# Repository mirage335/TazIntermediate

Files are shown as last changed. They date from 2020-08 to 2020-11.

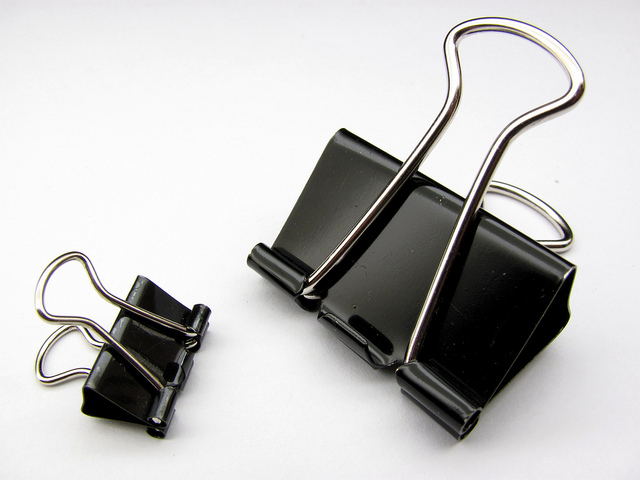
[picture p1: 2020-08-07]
_experimental/0100-Bundle/0165-Slab-slabAlternative-binderClipShim/_ref/BinderClip-f2otZE/orig/binder-clip.jpg

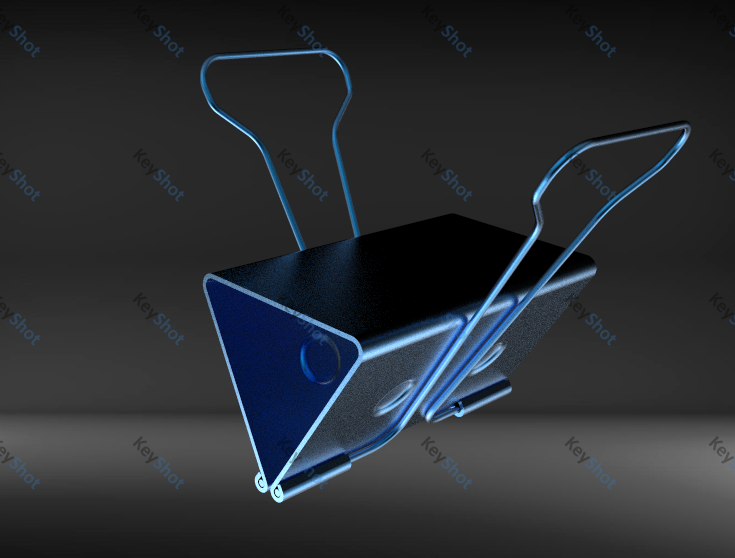
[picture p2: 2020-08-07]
_experimental/0100-Bundle/0165-Slab-slabAlternative-binderClipShim/_ref/BinderClip-f2otZE/orig/Capture.PNG

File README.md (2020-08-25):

Copyright (C) 2020- mirage335
See the end of the file for license conditions.
See license.txt for TazIntermediate license conditions.

A 3D printer system prioritizing cost-effectiveness and familiarity for industrial users accustomed to LulzBot Taz printers. Designed to balance similar or only slightly higher capital cost for for higher throughput, higher quality, and substantially lower maintence.

# Usage

Step-by-step assembly and maintenance instructions are provided, derived from the detailed design files.

Please read "_doc/TazIntermediate_serviceManual.pdf" .

# Distribution

REPUTABLE PROVIDERS OF TazIntermediate HARDWARE AND DESIGN FILES SHOULD INCLUDE IN YOUR ORDER A VERIFIABLE SERIAL NUMBER, GIT HASH, AND FULL COPY OF THE DESIGN FILES WITH ANY MODIFICATIONS.

Beware many of the assembly steps require careful attention to preloading, equal length cuts, strict order of operations, and correct alloy/tempering, among other things, for expected precision, accuracy, and durability. Intentionally little redundancy is available to compensate for poor quality components.

Consider providing end-users an entire copy of this repository with all submodules, in addition to PDF documents. Physical SDCard/USB flash devices may be suitable for the repository, printed hardcopy may be suitable for the PDF documents.

# Design

Inspired by the LulzBot Taz5 printer. Substantially similar to TazStiff, TazUp, Taz_Mega. TazIntermediate mostly serves to reduce new assembly time and wiring complexity.

Existing TazStiff printers should continue to offer similar performance and maintenance characteristics to TazIntermediate printers.

# Redistribution and Preservation

Entire 'recursive' clones of this repository with all submodules may be appropriate for redistribution and preservation.

# Safety

INTENDED FOR INDUSTRIAL USERS.
Internal wiring layout differs significantly from typical consumer 3D printers. In particular, contrary to typical RAMBo motherboard expectations, Vsys directly from PSU is used for Hotend power, and may be unfused. Reverse connection may present unfused (all RAMBo motherboard fuses bypassed) short-circuit load exceeding 20A, severely overloading MOSFET, wiring, and connectors.

Consider adding fiberglass or silica high-temperature sleeving to wiring near hotend.

Use external balancer with LiPo batteries. Cheaply available from HobbyKing among other places.

Not Ethernet compatible, will destroy network hardware.

Do not unplug powered steppers.

Beware common grounding and other wiring issues.

ClassIV lasers are extraordinarily hazardous. Backscatter from the projected spot alone is sufficient to slice a retina. Avoid exposure, and wear eye protection.

Ground-referenced voltage (ie. wall current) applied to Vsys/Vee is NOT guaranteed to remain isolated from other circuits. Spark gap surge protectors specifically, among other faults, are expected to allow sustained connection of high-voltage ground-referenced current to all other circuits.

Testing all essential high current circuits to 30% above requirements is recommended. Such testing has not necessarily been performed. Any particular circuit may not have been designed to accommodate any significant current carrying capacity. Oil immersion may increase useful ampacity, though the risk of dissolution or fire must be considered carefully. Design goals are made on a best effort basis only, suggested but not guaranteed for further development, particularly for short narrow traces.
GenericRap and derivative PCBs - Typically 5A power. Between XT60 Connectors, 40A power.
Solderless Breadboard - Typically 3A per contact. Typically >6A total to gold, tin, lead or similarly plated square pin header 'power feeder' as used by GenericRap.
Wrapping Wire 30AWG "Kynar" Insulated - Typically 6A per wire.

Fire suppression or low flammability products may be mentioned for consideration of further development only. None are specifically recommended for any situation, none may have been tested in any relevant application, and no claim of effectiveness is made.

No claim of liability is made by anyone. Your accident is your accident. Use common sense, and follow all regulations. If you don't understand the safety features and limitations, don't use this circuitry or anything similar.

# FutureWork

# Reference

https://en.wikipedia.org/wiki/Point-to-point_construction

https://www.mcmaster.com/high-temperature-sleeving/

https://www.mcmaster.com/high-temperature-sleeving/fiberglass-high-temperature-sleeving/

https://www.mcmaster.com/high-temperature-sleeving/expandable-electrical-insulating-tube-sleeving/

https://e3d-online.com/products/fibreglass-sleeving-for-insulating-thermistors-100mm

https://www.mcmaster.com/high-temperature-sleeving/silica-high-temperature-sleeving/

# Directory Specification

Consider keeping a copy of this specification alongside relevant projects for reference.

Please regard as a loose specification intended to offer unallocated regions for expansion and subordinate to any improvements that may be found in actual implementations.

Projects which may be assembled into larger projects, if sufficiently well-developed, should include their own appropriate directories, rather than referencing files shared within larger projects. That is to say, a sort of 'static linking' approach is strongly recommended.

Numbered directories with '[z]-' in their prefix and a '/' may substitute the '/' for either a '-' or separate directories.

Numbered directories of top-directories may be placed alongside top-directories if desired. Numbering scheme is intended to minimize conflicts.

Templates should populate only the most usual directories. Not all directories need be populated for a project.

```

_lib	- software, records, etc, typically uniquely needed by specific CAD model

00[00]-RESERVED (do NOT use)

01[00]-Bundle
	0110-Frames
	0150-Actuators
	0151[z]-Thruster/Driver
		Components only used for these?
		Screws used within these?
	0160-Tools
		Nozzle
		Hot-End
		Cold-End
		Extension (Bowden Tube)
	0162-Supplementary
		Filament Storage
	0165-Slab (workpiece mounting surface)
	0170-Tray (surface to mount electronics and similar)
	0172-Rack (enclosure for electronics and similar, and/or junction box)
	0175-Cabinet (arbitrary storage)

11[00]-Structural (Passive, Cut To Size)
	1110[z]-Extrusions/Timbers
		_resized
	1112[z]-Sheets/Panels/Plates (for frames only)
		_rescaled (PreDrilled only)
	1115-Backing (Table)

30[00]-Conveyance
	3030[z]-Shaft/Piston
	3032-LeadScrew
	3033[z]-Belts
	3035- to 3038- RESERVED (do NOT use)

35[00]-Couplings (including flexible, u-joints, etc)
	3530-LeadScrew_to_Motor

50[00]-Effectors
	5050[z]-Motors/Steppers/Servos
	5051[z]-RotaryBearings/RotaryShims
	
	5052[z]-NutBlocks/PlatesEffectors/BracketsEffectors (typically belt tie-down points), etc.
	5053-RESERVED
	
	5054[z]-Guides (Wheels/Bushings/LinearBearings)
	
	5055-Pulleys
	5056-Gears
	
	5058-Limit Switch

55[00]-RESERVED (do NOT use)

(6000 RESERVED)

(7000 RESERVED)

80[00]-Endpoints
	8080-Plug
		RJ45
		misc
	8081-Jack
		RJ45
		misc
	8082-RESERVED (do NOT use)
	8083-RESERVED (do NOT use)

85[00]-Dissipator
	8580-Fans
	8581-Pump
	8582-Heatsink
	8585-Radiator

9000-Miscellaneous
	9090z-Screws/Bolts
	9095-frequent (most frequently used)
	9099-Misc
		zMisc (unsortred, typically uniquely needed by specific CAD model)

9100-KEEPOUT (solid objects used to mark regions reserved for future use)

94[00]
to
98[00]
	RESERVED for future use

99[00]-import
	RESERVED for future use

```

# Third-Party Copyright Notices

Third-Party copyrights are noted within text files alongside directories containing the original files, and/or within text files alongside directories containing the modified files, and/or within version control commit history.

Some copyright licenses have specific requirements, and some authors have specific requests, to prominently display copyright notices - these are included here.

However, the manner some or all of these third-party files are used may in fact be fair use, in which case the third-party licenses would not in fact have any effect on the license requirements for the otherwise possibly derivative project.

"
This design incorporates OpenBuilds, LLC design work(s) shared Open Source under the CC BY-SA 4.0 License.
"

# Copyright

This file is part of TazIntermediate.

TazIntermediate is free software: you can redistribute it and/or modify
it under the terms of the GNU General Public License as published by
the Free Software Foundation, either version 3 of the License, or
(at your option) any later version.

TazIntermediate is distributed in the hope that it will be useful,
but WITHOUT ANY WARRANTY; without even the implied warranty of
MERCHANTABILITY or FITNESS FOR A PARTICULAR PURPOSE.  See the
GNU General Public License for more details.

You should have received a copy of the GNU General Public License
along with TazIntermediate.  If not, see <http://www.gnu.org/licenses/>.

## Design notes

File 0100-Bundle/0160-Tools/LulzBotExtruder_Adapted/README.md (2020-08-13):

'Stock' is expected to be workable as-is, though rigidity might be a little less due to use of plastic. This may or may not be significant.

'Bare' strictly considered experimental due to imprecise cooling mounting dimensions due to lack of matching accurate blower fan model for reference. Also for this reason the 'LulzBotExtruder_Block' has not been exported to other formats (ie. STEP, STL).

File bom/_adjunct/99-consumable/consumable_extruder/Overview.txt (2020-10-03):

ATC Semitec 104GT-2
	UNPROVEN - https://www.amazon.com/Gikfun-Semitic-104GT-2-Thermistor-Printer/dp/B00UFBIRVI/

6mm x 20mm 24V Heater Cartridge >30W (>8Ohm, <72W, 3A)
	https://www.amazon.com/BCZAMD-Upgraded-Cartridge-Accessories-Extruders/dp/B07SYZ3LGB/

PTFE Shrink (Hypothetical)
	https://www.mcmaster.com/7960K231/

>1mm >0.040in PTFE Sleeving (Thermistor) or Minimum-Size Fiberglass Sleeving
	~0.071in OD Expected _IF_ PTFE
	https://www.mcmaster.com/5335K15/
	https://www.mcmaster.com/7324T11/
	https://www.mcmaster.com/87675K1/

>2mm >1/8in >0.080in Fiberglass Sleeving
	https://www.mcmaster.com/2573K42/
	https://www.mcmaster.com/7324T12/
	https://www.mcmaster.com/87675K2/

>4mm >3/16in >0.150in Fiberglass Sleeving
	https://www.mcmaster.com/2573K43/
	https://www.mcmaster.com/7324T13/
	https://www.mcmaster.com/88175K32/

_Info_

24v Ceramic Heater Cartridge
	1x heater cartridge 24V 30W Heater cartridge needs 23cm leads with no connectors on end
	24V/19Ohm 6mm x 20mm

NTC 100k Thermistor
	1x Semitec GT2 thermistor (100kOhm type) Thermistor needs 23cm leads with no connectors on end
	1 100k ATC Semitec 104GT-2 thermistor, terminated with bare connector pin
	EPCOS B57560G104F NTC Thermistor (most used thermistor in the reprap community)
	#define TEMP_SENSOR_1 5
	// 5 is 100K thermistor - ATC Semitec 104GT-2 (Used in ParCan & J-Head) (4.7k pullup)
	5 : 100K thermistor - ATC Semitec 104GT-2/104NT-4-R025H42G (Used in ParCan, J-Head, and E3D) (4.7k pullup)

_Reference_
https://www.lulzbot.com/store/parts/lulzbot-v2-hexagon-hot-end
https://www.amazon.com/RepRapDiscount-Hexagon-Hotend-Heater-Cartridge/dp/B00W4AIFBK
http://www.reprapdiscount.com/hotends/67-hexagon-hotend-set.html

http://www.makerfarm.com/index.php/hot-ends/hot-end-parts/100k-thermistor.html

https://itworks3d.com/product/hexagon-hotend-assembly-2/

https://itworks3d.com/product/thermistor-3d-printer/
https://itworks3d.com/product/ceramic-heater-cartridge-hexagon-hotend/

https://smile.amazon.com/Ceramic-Cartridge-Compatible-Printer-Creality/dp/B08B4DVN2V/

https://download.lulzbot.com/TAZ/6.01/software/firmware/Marlin_TAZ-6.01_Single_v1.0.2.20_01d5281/Marlin/Configuration.h
https://github.com/MarlinFirmware/Configurations/blob/import-2.0.x/config/default/Configuration.h

https://aus3d.com.au/e3d-thermistor-cartridge

https://www.mcmaster.com/ptfe-heat-shrink-tubing/
https://www.mcmaster.com/high-temperature-sleeving/
https://www.mcmaster.com/wire-protection-sleeving/expandable-electrical-insulating-tube-sleeving/
https://www.mcmaster.com/wire-protection-sleeving/fiberglass-high-temperature-sleeving/

https://reprapltd.com/reprappro/documentation/fisher-1/hot-end-assembly/index.html

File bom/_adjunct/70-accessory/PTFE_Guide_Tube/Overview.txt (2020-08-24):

A guide tube should be mounted at a fixed location on the machine to prevent filament from pulling back on the tool during high speed movement.

If this tube may be repurposed as a bowden tube, Capricorn XS tubing should be used with Capricorn fittings.

Filament Spool...
Diameter <200mm
Thickness <80mm

_Reference_

https://www.captubes.com/shop/#!/2-Meter-XS-Low-Friction-2-85mm-Bowden-Tubing/p/103183531/category=23214267

https://www.captubes.com/shop/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

https://www.captubes.com/shop/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
https://www.captubes.com/shop/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

https://smile.amazon.com/PTFE-Teflon-tubing-5ft-Filament/dp/B07B8KMNQN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

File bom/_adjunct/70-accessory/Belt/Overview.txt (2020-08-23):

_Reference_
https://openbuildspartstore.com/gt2-2m-timing-belt-by-the-foot/
https://openbuildspartstore.com/timing-belt-tension-torsion-spring/

https://smile.amazon.com/Mercurry-Meters-timing-Rostock-GT2-6mm/dp/B01E91K4N8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

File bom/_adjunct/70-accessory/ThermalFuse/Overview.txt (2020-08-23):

_Reference_
https://smile.amazon.com/uxcell-Celsius-Circuit-Temperature-Ceramics/dp/B07XKNN3GV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
https://smile.amazon.com/uxcell-Celsius-Circuit-Temperature-Ceramics/dp/B07XKP316Z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

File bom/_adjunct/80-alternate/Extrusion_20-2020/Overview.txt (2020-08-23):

	20series Extrusion
$17.32/2440mm
Price of 2440mm exactly was an exact match between Amazon and 8020 website, although Amazon site shows $14.73 shipping cost added.
https://8020.net/20-2020.html#
https://smile.amazon.com/80-20-20-2020-T-Slotted-Extrusion/dp/B001F0I3G2

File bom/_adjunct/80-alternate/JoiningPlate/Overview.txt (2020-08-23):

	Joining Plate 90deg
Thickness claimed 3.6mm, possibly less than 4mm claimed by OpenBuilds equivalent.
https://smile.amazon.com/Boeray-10pcs-Joining-Aluminum-Profile/dp/B01H4VY6VG

	Joining Plate T
CLaimed major dimensions match claimed by OpenBuilds equivalent.
https://smile.amazon.com/Boeray-10pcs-Joining-Aluminum-Profile/dp/B01H4YPT64/

	Joining Plate L
May or may not simplify slab mounting at expense of rigidity.
https://8020.net/20-4081.html

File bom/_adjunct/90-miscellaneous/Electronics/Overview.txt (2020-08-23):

*) RAMBO Motherboard (~$150)
*) PatchRap (~$150)

*) Enclosures. Prefer at least highly water resistant junction boxes with transparent lids.

*) PSU. 24V 20A.

*) Wiring. Cat5E entire bundle as single wire to heated bed, or high-temperature silicone wire. Cat6A RJ45 interconnect, always same length.

*) XT60, RJ45 Keystone Jacks, Breadboards.

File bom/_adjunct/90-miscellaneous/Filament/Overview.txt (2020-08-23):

Clear Polycarbonate and Clear TPU are recommended for such parts as the Stock Extruder Mount, custom probe mounts (if not metal), and flexible shims (used to compress lock collars used on ACME Threaded Rods).

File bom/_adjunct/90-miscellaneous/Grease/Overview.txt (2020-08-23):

V-Slot Linear Bearing surfaces, V-Wheel Ball Bearings (spread on top before assembly), and Z-axis grease points must only use Super Lube 41150 Synthetic Grease grease.

NEMA17 motor ball bearings may or may not benefit from grease. Do not attempt to use silicone based grease - the higher friction displacing any factory oil may cause more harm than benefit.

https://smile.amazon.com/dp/B0042FG74W/

Only belts must only use silicone based PTFE grease, due to chemical compatibility with neoprene. Severe wear to belt and pulleys will result without this specific grease..
https://smile.amazon.com/gp/product/B0081JE0OO/

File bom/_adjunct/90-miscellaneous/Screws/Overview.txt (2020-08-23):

*) M5 Screws
Torque applied should be maximum possible before damaging the threads of the Tee nut or screw. If necessary, practice a few trial runs to determine equivalent drill clutch setting or get a manual feel for maxium torque. Maximum torque ensures maximum pressure, ensuring long-term stability and mitigating vibration affecting different parts of the machine separately.

In addition to the estimated screws and related components (ie. nuts), driver bits should be regarded as consumable at a rate of at least one or two per machine. Buy hex 3mm driver bit and hex 3mm 'key wrench' packs, and grind down as necessary. Worn bits are more likely to cam out, risking severe damage or inconvenience.

M5 (and less likely M3) drill tap is also required.

Small quantities of M3 screws may be commonly needed by Tool and Slab.

At least equal number of Tee nuts required.

183 Typical guesstimate
	M5*8mm measured
32 1/4inch plate guesstimate
	M5*12mm measured

	Typical
		*6
	
	Idler
		M5x25mm (+0)
			* 2 (+0)
	V-Wheel Axle
		* 12
	
	AxisY
		1/4inch plate
			* 8
		Typical
			* 12
	
	Slab
		Belt Tension
			* 2
		Typical
			* 34
	
	Axis_X-Actuator
		Typical
			* 4
	
	AxisZ
		Typical
			* 65
		1/4inch plate
			* 20
	
	AxisZ_Truck-Double
		Typical
			* 24
		Anti-Backlash
			* 4
	
	LulzBotExtruder_Example_Stock
		1/4inch plate
			* 4
		Typical
			* 38

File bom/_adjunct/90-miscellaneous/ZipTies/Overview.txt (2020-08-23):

Zip Ties... are strongly recommended for a variety of uses.

Specifically, attachment of extruder chasis fan, attachment of depth probe, and binding wiring/tubing to machine for strain relief, may require zip ties.

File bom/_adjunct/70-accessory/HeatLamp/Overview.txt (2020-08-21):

As a reminder, pairs of  20W 12V halogen lights may be used in place of or in addition to direct bed heating. This may have the advantage of better ensuring the entire workpiece remains at thermoplastic temperature during printing, reducing such things as 'warping'.

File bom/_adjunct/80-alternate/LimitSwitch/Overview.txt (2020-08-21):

Micro limit switch plates may become difficult to obtain. Rather than having them custom fabricated, it may be worth trying the new 'Xtension Limit Switch Kit' from OpenBuilds in limited applications where they fit and the additional circuitry may be desirable.

_Reference_
https://openbuildspartstore.com/xtension-limit-switch-kit/

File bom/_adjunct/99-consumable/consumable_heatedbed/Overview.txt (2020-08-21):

PEI Printing Surface 10mil 11.8in x 11.8in (300mm x 300mm)
	https://www.mcmaster.com/3697N36/

3M adhesive sheet 5mil
	https://www.amazon.com/Gizmo-Dorks-Adhesive-Transfer-Sheets/dp/B01HP2CEG8

2000grit sandpaper (use sparingly)
	https://www.amazon.com/3M-32044-Imperial-Wetordry-Sheet/dp/B0002MSY90/

Springs
	Bed leveling springs, and possibly extruder idler springs, for Taz5, Mini, are apparently C0180-020-0750-M .

Heater
	Heater is apparently either Tepco SHS80989 or National Plastic Heater NPH PC-BD0027.

Other
	Binder clips (assorted).
	Isopropyl alcohol 91% (both lower and higher concentration expected to be less effective).
	Paper towels.
	M5 tee nuts (in case of damaged threads).
	Various M3 screws.

_Reference_
http://devel.lulzbot.com/retail_parts/LulzBot_TAZ_Etched_Modular_Print_Bed_Heater_KT-HB0014/LulzBot_TAZ_Etched_Modular_Print_Bed_Heater_KT-HB0014_BoM.csv

https://www.lulzbot.com/store/parts/24v-silicone-heater

https://reprap.org/wiki/PEI_build_surface
https://www.amazon.com/Gizmo-Dorks-Adhesive-Transfer-Sheets/dp/B01HP2CEG8

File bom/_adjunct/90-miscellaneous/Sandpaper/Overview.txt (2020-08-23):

Multiple grades of sandpaper will be needed from perhaps 60grit, to 2000grit. Specifically this is usually required to correctly narrow down the ACME threaded rod to exactly fit rotary ball bearings.

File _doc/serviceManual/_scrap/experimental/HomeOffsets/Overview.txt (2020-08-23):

_Reference_
https://marlinfw.org/docs/gcode/M206.html
https://marlinfw.org/docs/gcode/M428.html
https://marlinfw.org/docs/gcode/G034.html

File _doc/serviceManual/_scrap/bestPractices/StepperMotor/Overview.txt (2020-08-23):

	NEMA 17 2.8mH 1.8
SY42STH47-1504A
55.0 N·cm
2.8 V, 1.5A, 2.8mH
'5 mm single'
1.8deg 200Steps/Rev
47 mm Length

OpenBuilds stepper motors currently seem to be roughly comparable.

Require closely comparable and reputable stepper motor. That is not a recommendation when precision, torque, or speed, may be paramount.

Specific model SY42STH47-1504A stepper motor as used by AlephObjects for stock Taz machines, has demonstrated full precision driving of entire linear actuator as well as high torque at high speed.

*) Measured by TazMega microscope to drive lead screws at approximately 3um precision, mechanically realizing full 1/16 microstepping resolution.
*) Speeds of >>100mm/s with TazMega lead screws.
*) Speeds of >>240mm/s with TazStiff belts.

	40mm northbridge heatsink
	Arctic Silver 7g Premium Silver Thermal Cooling Adhesive Set (ASTA-7G)

If additional performance is required, any kind of 40mm northbridge heatsinks may be attached with thermal epoxy.

Beware active (with fans) heatsinks may or may not cause poor print quality (including poor adhesion) due to additional vibration - this has not been evaluated extensively enough.

_Plastic Shrinkage Compensation_
Beware LulzBot machines typically are configured to 100.5 steps per mm. Any printers used industrially along such stock machines should include the same compensation, unless these machines are also to be used with other manufacturing tools (eg. laser) .

_Trivia_
Lead Screw is 8mm/Rev
1/16microstep
400microsteps/mm

16tooth pulley
2mm belt pitch
200Steps/Rev
1/16microstep
100microsteps/mm
6.25fullSteps/mm
80mm/s Maximum Torque (Hypothetical)
640mm/s Half Torque (Theoretical, 4000PPS)
400mm/s 2500PPS

14tooth pulley
2mm belt pitch
200Steps/Rev
1/16microstep
114.29microsteps/mm
7.14fullSteps/mm
~80mm/s Maximum Torque (Hypothetical)
~640mm/s Half Torque (Theoretical, 4000PPS)
~400mm/s 2500PPS
12mm (~1cm) Diameter
~2.5kg Half Torque
~2kg Load (presumed)

Recommended maximum X/Y travel speed is >660mm/s (~0.5m/s) (theoretical) up to 900mm/s. Recommended maximum acceleration is >6000mm/s^2 (~0.5g) up to 9000mm/s^2 or 7500mm/s^2 . Acceleration of 3000mm/s is suggested if necessary to reduce surface defects due to belt slippage (theoretical).

Jerk, as a threshold before acceleration is applied, is suggested as a maximum of 20mm/s, but may be beneficial to reduce as far as possible.

Acceleration of 1000mm/s^2 (0.1g) is expected to reach ~480mm/s speed mid-way between a 300mm travel distance (deceleration taking most of the remaining travel distance).

Lulzbot known defaults...
#define DEFAULT_AXIS_STEPS_PER_UNIT   {100.5,100.5,1600,830}  // default steps per unit for LulzBot TAZ
#define DEFAULT_MAX_FEEDRATE          {800, 800, 3, 40}    // (mm/sec)
#define DEFAULT_MAX_ACCELERATION      {9000,9000,100,10000}    // X, Y, Z, E maximum start speed for accelerated moves.

#define DEFAULT_ACCELERATION          500    // X, Y, Z and E max acceleration in mm/s^2 for printing moves
#define DEFAULT_RETRACT_ACCELERATION  3000   // X, Y, Z and E max acceleration in mm/s^2 for retracts
#define DEFAULT_XYJERK                8.0    // (mm/sec)
#define DEFAULT_ZJERK                 0.4     // (mm/sec)
#define DEFAULT_EJERK                 10.0    // (mm/sec)

_Reference_
https://www.lulzbot.com/store/parts/nema-17-stepper-motor
http://download.lulzbot.com/AO-100/hardware/electronics/spec_sheets/SY42STH47-1504A_stepperMotors.pdf
https://reprap.org/wiki/Stepper_motor
https://reprap.org/wiki/NEMA_17_Stepper_motor

https://openbuildspartstore.com/nema-17-stepper-motor/
http://motechmotor.com/productDetail-0104-32.html
	MT-1704HS168A-0B

https://www.amazon.com/Iverntech-Stepper-Printer-Machine-Robotics/dp/B07PS4BMSN/
https://www.amazon.com/Torque-Bipolar-Stepper-Motor-Extruder/dp/B00PNEQUZ2/
https://www.amazon.com/STEPPERONLINE-Stepper-Bipolar-Connector-compatible/dp/B00PNEQKC0/
https://www.amazon.com/Stepper-Quimat-Connector-Mounting-Brackets/dp/B06XR8Q5Y2/
	Possibly worth evaluating. Beware high inductance may or may not impact speed.

https://openbuildspartstore.com/nema-23-stepper-motor-high-torque-series/

https://forum.lulzbot.com/t/steps-unit-right-or-wrong/1830

https://blog.prusaprinters.org/calculator_3416/
https://dyzedesign.com/2016/10/printing-300-mm-s-part-1-basics-hardware/

https://www.youtube.com/watch?v=7bCYyWF9Wb4
https://www.youtube.com/watch?v=alsjrXy08jU

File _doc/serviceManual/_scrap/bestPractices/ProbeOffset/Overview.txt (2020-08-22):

_Machine Panel_
Z-Offset > Store Settings

_OctoPrint_
Read Z Offset
Write Z Offset (manually modified)
Save EEPROM Settings (if necessary)

"
Set the XYZ distance from the nozzle to the probe trigger-point.

    The easiest way to get the Z offset value is to:
    Home the Z axis.
    Raise Z and deploy the probe.
    Move Z down slowly until the probe triggers.
    Take the current Z value and negate it. (5.2 => -5.2)
    Set with M851 Z-5.2 and #define Z_PROBE_OFFSET_FROM_EXTRUDER -5.2.

For X and Y you have to measure the distance.
"

_Reference_
https://marlinfw.org/docs/gcode/M851.html
https://www.youtube.com/watch?v=Q5M7DvdMcew

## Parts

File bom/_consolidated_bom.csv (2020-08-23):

#item | dstpn | mult | qty | dst | mark | provider | path
20series-1x1_160mm.fcstd |  | 2 | 0 | 8020
20series-1x1_500mm.fcstd |  | 4 | 0 | 8020 | 20-2020-2440mm
20series-1x1_545mm.fcstd |  | 4 | 0 | 8020 | 20-2020-2440mm
20series-1x1-60mm.fcstd |  | 1 | 0 | 8020
20series-1x1-crossbar.fcstd |  | 1 | 0 | 8020
20series-1x1-postX.fcstd |  | 2 | 0 | 8020
20series-1x1-postY.fcstd |  | 2 | 0 | 8020 | 20-2020-2440mm
8mm Acme Nut Plate.step |  | 4 | 0 | OpenBuilds |  |  |  | $6.99
Aluminum Spacer 1.5in.step |  | 6 | 0 | OpenBuilds
Ball Bearing 5 x 16 x 5.step |  | 28 | 0 |  |  |  |  | +0
Ball Bearing 8 x 16 x 5.step |  | 4 | 0 | OpenBuilds |  |  |  | $0.99
Black Angle Corner Connector.step |  | 21 | 0 | OpenBuilds |  |  |  | $2.99
Cast Corner Bracket.step |  | 7 | 0 | OpenBuilds |  |  |  | $1.49
Cube Corner Connector.step |  | 6 | 0 | OpenBuilds |  |  |  | $3.49
Eccentric Spacer 6mm.step |  | 12 | 0 | OpenBuilds |  |  |  | $1.99
Flexible Coupling 5mm x 8mm.step |  | 2 | 0 | OpenBuilds |  |  |  | $6.99
gantryPlate.fcstd |  | 5 | 0 | eMachineShop |  |  |  | $31.00
Grease Nipple M6.STEP |  | 2 | 0 | Amazon |  |  |  | $0.50
GT2 Timing Pulley 14 Tooth.step |  | 2 | 0 | OpenBuilds |  |  |  | $5.29
Idler Pulley Plate.step |  | 2 | 0 | OpenBuilds |  |  |  | $6.99
Joining Plate 90 Degree.step |  | 14 | 0 | OpenBuilds |  |  |  | $4.99
Joining Plate T.step |  | 7 | 0 | OpenBuilds |  |  |  | $3.99
L Bracket Triple.step |  | 3 | 0 | OpenBuilds |  |  |  | $1.99
LeadScrew_8mm-520mm.fcstd |  | 2 | 0 | OpenBuilds |  |  |  | $21.99
Lock Collar 8mm.step |  | 4 | 0 | OpenBuilds |  |  |  | $0.99
LulzBotExtruder_Carriage_Block.fcstd |  | 1 | 0
LulzBot_Extruder-LulzBot_Mount |  | 1 | 0 |  |  |  |  | $200.00
Micro Limit Switch Plate.step |  | 3 | 0 | OpenBuilds |  |  |  | $7.00
Motor Mount Plate Nema 17.step |  | 2 | 0 | OpenBuilds |  |  |  | $6.99
Nema 17 Stepper Motor.step |  | 4 | 0 | OpenBuilds |  |  |  | $17.99
Nylon Spacer 0.125in.step |  | 2 | 0 |  |  |  |  | +0
paper binder1.fcstd |  | 4 | 0 | Amazon
Precision Shim 10 x 5 x 1.step |  | 2 | 0 |  |  |  |  | +0
Precision Shim 8 x 5 x 1.step |  | 24 | 0 |  |  |  |  | +0
ShimFlexiblePreload-8mm.fcstd |  | 2 | 0
Shim Washer 8mm.step |  | 6 | 0 | OpenBuilds | Shim - 12 x 8 x 1mm |  |  | $0.29
Smooth Idler Pulley Wheel.step |  | 2 | 0 | OpenBuilds |  |  |  | $5.99
SS_01GL_E.FCStd |  | 3 | 0 |  | LimitSwitch
TAZ 5 Y Plate Assembly V0.21-slab_legacy_only.step |  | 1 | 0 |  |  |  |  | $200
ThinHexNut-Modified Nylon Insert Lock Nut M5.step |  | 12 | 0 | OpenBuilds |  |  |  | $0.10
Threaded Rod Plate Nema 17-Idler.fcstd |  | 2 | 0 | OpenBuilds |  |  |  | $7.99
Threaded Rod Plate Nema 17.step |  | 2 | 0 | OpenBuilds |  |  |  | $7.99
V-Slot 20x20x140mm.FCStd |  | 3 | 0 | OpenBuilds |  |  |  | x2
V-Slot 20x20x220mm.FCStd |  | 1 | 0 | OpenBuilds |  |  |  | x1
V-Slot 20x20x40mm.FCStd |  | 1 | 0 | OpenBuilds |  |  |  | x2
V-Slot 20x20x540mm.FCStd |  | 2 | 0 | OpenBuilds |  |  |  | x1
V-Slot 20x20x60mm.FCStd |  | 2 | 0 | OpenBuilds |  |  |  | x2
V-Slot 20x20x80mm.FCStd |  | 1 | 0 | OpenBuilds |  |  |  | x2
V-Slot 20x40x120mm.FCStd |  | 2 | 0 | OpenBuilds
V-Slot 20x40x500mm.FCStd |  | 2 | 0 | OpenBuilds |  |  |  | $6.99
V-Slot 20x60x220mm.fcstd |  | 1 | 0 | OpenBuilds
V-Slot 20x60x760mm.fcstd |  | 1 | 0 | OpenBuilds | 20x60 x1000mm
Xtreme Solid V Wheel.step |  | 12 | 0 | OpenBuilds |  |  |  | $6.99
XYplate.fcstd |  | 1 | 0 | eMachineShop |  |  |  | $72.00

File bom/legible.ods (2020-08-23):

#item | dstpn | mult | qty | dst | mark | provider | path |  | SPLIT | TOTAL | NOTES
20series-1x1_160mm.fcstd |  | 2 | 0 | 8020 |  |  |  | x |  | $0.00
20series-1x1_500mm.fcstd |  | 4 | 0 | 8020 | 20-2020-2440mm |  |  | x | $17.32 | $17.32
20series-1x1_545mm.fcstd |  | 4 | 0 | 8020 | 20-2020-2440mm |  |  | x | $17.32 | $17.32
20series-1x1-60mm.fcstd |  | 1 | 0 | 8020 |  |  |  | x |  | $0.00
20series-1x1-crossbar.fcstd |  | 1 | 0 | 8020 |  |  |  | x |  | $0.00
20series-1x1-postX.fcstd |  | 2 | 0 | 8020 |  |  |  | x |  | $0.00
20series-1x1-postY.fcstd |  | 2 | 0 | 8020 | 20-2020-2440mm |  |  | x | $17.32 | $17.32
8mm Acme Nut Plate.step |  | 4 | 0 | OpenBuilds |  |  |  | $6.99 |  | $27.96
Aluminum Spacer 1.5in.step |  | 6 | 0 | OpenBuilds |  |  |  |  | $6.49 | $6.49
Ball Bearing 5 x 16 x 5.step |  | 28 | 0 |  |  |  |  | $0.00 |  | $0.00 | 24 used by wheels, 4 used by belt idlers
Ball Bearing 8 x 16 x 5.step |  | 4 | 0 | OpenBuilds |  |  |  | $0.99 |  | $3.96
Black Angle Corner Connector.step |  | 21 | 0 | OpenBuilds |  |  |  | $2.99 |  | $62.79
Cast Corner Bracket.step |  | 7 | 0 | OpenBuilds |  |  |  | $1.49 |  | $10.43
Cube Corner Connector.step |  | 6 | 0 | OpenBuilds |  |  |  | $3.49 |  | $20.94
Eccentric Spacer 6mm.step |  | 12 | 0 | OpenBuilds |  |  |  | $1.99 |  | $23.88
Flexible Coupling 5mm x 8mm.step |  | 2 | 0 | OpenBuilds |  |  |  | $6.99 |  | $13.98
gantryPlate.fcstd |  | 5 | 0 | eMachineShop |  |  |  | $31.00 |  | $155.00
Grease Nipple M6.STEP |  | 2 | 0 | Amazon |  |  |  | $0.50 |  | $1.00
GT2 Timing Pulley 14 Tooth.step |  | 2 | 0 | OpenBuilds |  |  |  | $5.29 |  | $10.58
Idler Pulley Plate.step |  | 2 | 0 | OpenBuilds |  |  |  | $6.99 |  | $13.98
Joining Plate 90 Degree.step |  | 14 | 0 | OpenBuilds |  |  |  | $4.99 |  | $69.86
Joining Plate T.step |  | 7 | 0 | OpenBuilds |  |  |  | $3.99 |  | $27.93
L Bracket Triple.step |  | 3 | 0 | OpenBuilds |  |  |  | $1.99 |  | $5.97
LeadScrew_8mm-520mm.fcstd |  | 2 | 0 | OpenBuilds |  |  |  | $21.99 |  | $43.98
Lock Collar 8mm.step |  | 4 | 0 | OpenBuilds |  |  |  | $0.99 |  | $3.96
LulzBotExtruder_Carriage_Block.fcstd |  | 1 | 0 |  |  |  |  |  |  | $0.00
LulzBot_Extruder-LulzBot_Mount |  | 1 | 0 |  |  |  |  | $200.00 |  | $200.00
Micro Limit Switch Plate.step |  | 3 | 0 | OpenBuilds |  |  |  | $7.00 |  | $21.00
Motor Mount Plate Nema 17.step |  | 2 | 0 | OpenBuilds |  |  |  | $6.99 |  | $13.98
Nema 17 Stepper Motor.step |  | 4 | 0 | OpenBuilds |  |  |  | $17.99 |  | $71.96
Nylon Spacer 0.125in.step |  | 2 | 0 |  |  |  |  | $0.00 |  | $0.00
paper binder1.fcstd |  | 4 | 0 | Amazon |  |  |  |  |  | $0.00
Precision Shim 10 x 5 x 1.step |  | 2 | 0 |  |  |  |  | $0.00 |  | $0.00
Precision Shim 8 x 5 x 1.step |  | 24 | 0 |  |  |  |  | $0.00 |  | $0.00
ShimFlexiblePreload-8mm.fcstd |  | 2 | 0 |  |  |  |  |  |  | $0.00
Shim Washer 8mm.step |  | 6 | 0 | OpenBuilds | Shim - 12 x 8 x 1mm |  |  | $0.29 |  | $1.74
Smooth Idler Pulley Wheel.step |  | 2 | 0 | OpenBuilds |  |  |  | $5.99 |  | $11.98
SS_01GL_E.FCStd |  | 3 | 0 |  | LimitSwitch |  |  |  |  | $0.00
TAZ 5 Y Plate Assembly V0.21-slab_legacy_only.step |  | 1 | 0 |  |  |  |  | $200.00 |  | $200.00
ThinHexNut-Modified Nylon Insert Lock Nut M5.step |  | 12 | 0 | OpenBuilds |  |  |  | $0.10 |  | $1.20
Threaded Rod Plate Nema 17-Idler.fcstd |  | 2 | 0 | OpenBuilds |  |  |  | $7.99 |  | $15.98 | Modified - cut by saw.
Threaded Rod Plate Nema 17.step |  | 2 | 0 | OpenBuilds |  |  |  | $7.99 |  | $15.98
V-Slot 20x20x140mm.FCStd |  | 3 | 0 | OpenBuilds |  |  |  | x2 |  | $0.00
V-Slot 20x20x220mm.FCStd |  | 1 | 0 | OpenBuilds |  |  |  | x1 |  | $0.00
V-Slot 20x20x40mm.FCStd |  | 1 | 0 | OpenBuilds |  |  |  | x2 |  | $0.00
V-Slot 20x20x540mm.FCStd |  | 2 | 0 | OpenBuilds |  |  |  | x1 | $15.99 | $15.99
V-Slot 20x20x60mm.FCStd |  | 2 | 0 | OpenBuilds |  |  |  | x2 |  | $0.00
V-Slot 20x20x80mm.FCStd |  | 1 | 0 | OpenBuilds |  |  |  | x2 | $15.99 | $15.99
V-Slot 20x40x120mm.FCStd |  | 2 | 0 | OpenBuilds |  |  |  | x | 6.99 | $6.99
V-Slot 20x40x500mm.FCStd |  | 2 | 0 | OpenBuilds |  |  |  | $6.99 |  | $13.98
V-Slot 20x60x220mm.fcstd |  | 1 | 0 | OpenBuilds |  |  |  | x |  | $0.00
V-Slot 20x60x760mm.fcstd |  | 1 | 0 | OpenBuilds | 20x60 x1000mm |  |  | x | 19.49 | $19.49
Xtreme Solid V Wheel.step |  | 12 | 0 | OpenBuilds |  |  |  | $6.99 |  | $83.88
XYplate.fcstd |  | 1 | 0 | eMachineShop |  |  |  | $72.00 |  | $72.00
 |  |  |  |  |  |  |  |  |  | $1,336.79

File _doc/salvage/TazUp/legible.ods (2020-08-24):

#item | dstpn | mult | qty | dst | mark | provider | path |  | SPLIT | TOTAL | NOTES
20series-1x1_500mm.fcstd |  | 4 | 0 | 8020 | 20-2020-2440mm |  |  | x | $17.32 | $17.32
20series-1x1_545mm.fcstd |  | 4 | 0 | 8020 | 20-2020-2440mm |  |  | x | $17.32 | $17.32
gantryPlate.fcstd |  | 5 | 0 | eMachineShop |  |  |  | $31.00 |  | $155.00
Joining Plate 90 Degree.step |  | 8 | 0 | OpenBuilds |  |  |  | $4.99 |  | $39.92
LulzBot_Extruder-LulzBot_Mount |  | 1 | 0 |  |  |  |  | $200.00 |  | $200.00
Nema 17 Stepper Motor.step |  | 4 | 0 | OpenBuilds |  |  |  | $17.99 |  | $71.96
TAZ 5 Y Plate Assembly V0.21-slab_legacy_only.step |  | 1 | 0 |  |  |  |  | $200.00 |  | $200.00
XYplate.fcstd |  | 1 | 0 | eMachineShop |  |  |  | $72.00 |  | $72.00
 |  |  |  |  |  |  |  |  |  | $773.52

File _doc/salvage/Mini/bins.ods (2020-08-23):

#item | dstpn | mult | qty | dst | mark | provider | path | cost | SPLIT | TOTAL | NOTES
LulzBot_Extruder-LulzBot_Mount |  | 1 | 0 |  |  |  |  | $200.00 |  | $200.00
Nema 17 Stepper Motor.step |  | 4 | 0 | OpenBuilds |  |  |  | $17.99 |  | $71.96
RAMBO Motherboard |  | 1 |  |  |  |  |  | $150.00 |  | $150.00
 |  |  |  |  |  |  |  |  |  | $421.96

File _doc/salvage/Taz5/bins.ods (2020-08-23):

#item | dstpn | mult | qty | dst | mark | provider | path | cost | SPLIT | TOTAL | NOTES
20series-1x1_500mm.fcstd |  | 4 | 0 | 8020 | 20-2020-2440mm |  |  | x | $17.32 | $17.32
20series-1x1_545mm.fcstd |  | 4 | 0 | 8020 | 20-2020-2440mm |  |  | x | $17.32 | $17.32
LulzBot_Extruder-LulzBot_Mount |  | 1 | 0 |  |  |  |  | $200.00 |  | $200.00
Nema 17 Stepper Motor.step |  | 4 | 0 | OpenBuilds |  |  |  | $17.99 |  | $71.96
TAZ 5 Y Plate Assembly V0.21-slab_legacy_only.step |  | 1 | 0 |  |  |  |  | $200.00 |  | $200.00
RAMBO Motherboard |  | 1 |  |  |  |  |  | $150.00 |  | $150.00
24V PSU |  | 1 |  |  |  |  |  | $40.00 |  | $40.00
Belts |  |  |  |  |  |  |  |  |  | $0.00 | May not be of sufficient length to salvage.
Screws |  |  |  |  |  |  |  |  |  | $0.00 | Indeterminate.
 |  |  |  |  |  |  |  |  |  | $696.60

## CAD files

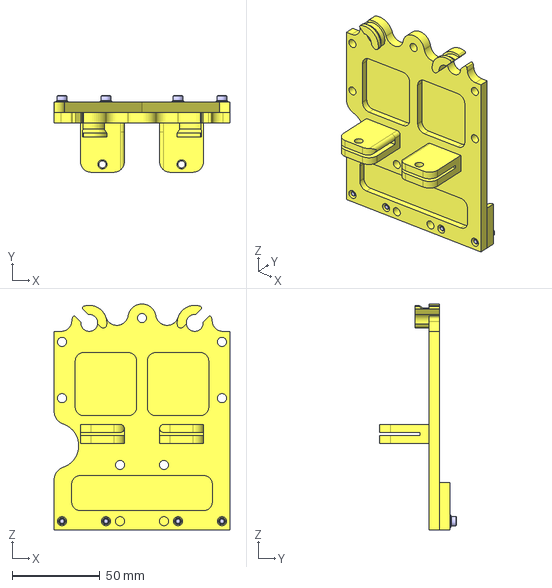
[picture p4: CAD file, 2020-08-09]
0100-Bundle/0160-Tools/LulzBotExtruder_Adapted/_ref/LulzBot_Extruder/TAZ 5 X Carriage Assembly V0.1/mod/TAZ 5 X Carriage Assembly V0.1_minimal.step
100.0 x 43.5 x 128.6 mm

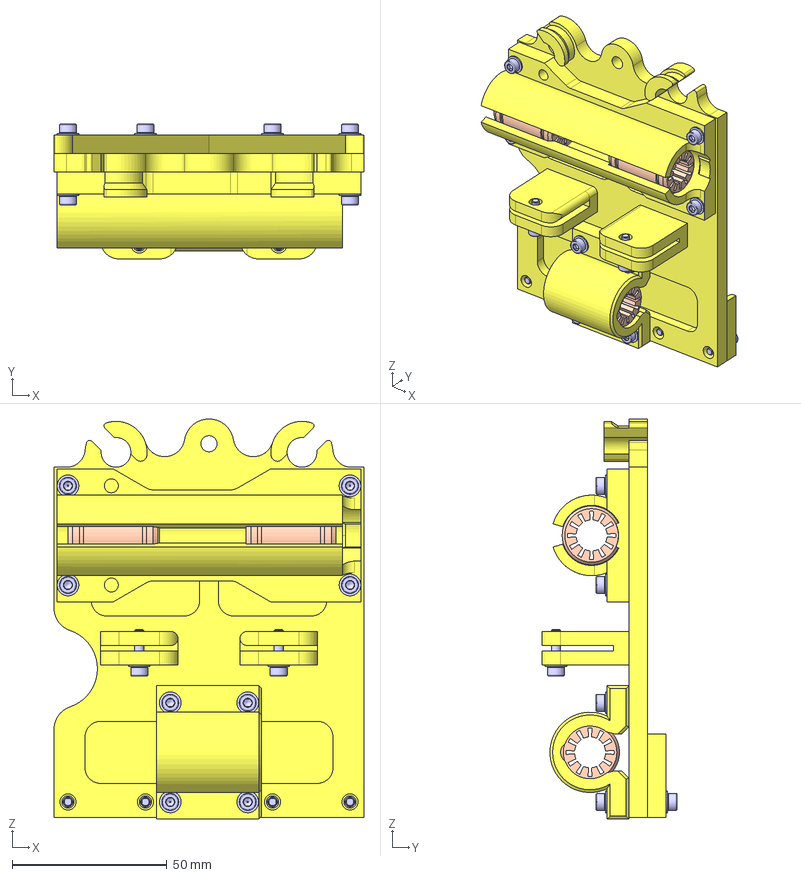
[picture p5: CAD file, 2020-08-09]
0100-Bundle/0160-Tools/LulzBotExtruder_Adapted/_ref/LulzBot_Extruder/TAZ 5 X Carriage Assembly V0.1/orig/TAZ 5 X Carriage Assembly V0.1.fcstd
100.0 x 43.5 x 129.1 mm
x_carriage_V2_0_fc0_1_01
Bearing_Holder_v1_1_b_fc0_1_01
x_carriage_guide_V1_0_fc0_1_01
double_bearing_holder_2_0_fc0_1_01
IGUS_RJM_01_10_01
IGUS_RJM_01_10_02
IGUS_RJM_01_10_03
M3_washer_02
M3_washer_03
M3_washer_04
M3_washer_05
M3_washer_06
M3_washer_07
M3_washer_08
M3_washer_09
M3_washer_10
M3_washer_11
M3_washer_12
M3_washer_13
M3x12_SHCS_02
M3x12_SHCS_03
M3x12_SHCS_04
M3x12_SHCS_05
M3x12_SHCS_06
M3x12_SHCS_07
M3x12_SHCS_08
M3x12_SHCS_09
M3x12_SHCS_10
M3x12_SHCS_11
M3x12_SHCS_12
M3x12_SHCS_13
M3_washer_14
M3_washer_15
M3x12_SHCS_14
M3x12_SHCS_15

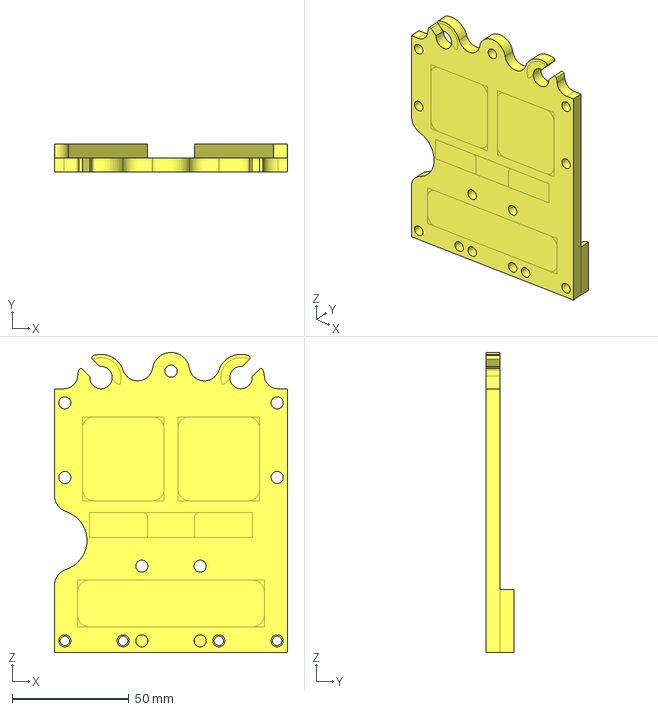
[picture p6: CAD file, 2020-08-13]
0100-Bundle/0160-Tools/LulzBotExtruder_Adapted/LulzBotExtruder_Carriage_Block/TAZ 5 X Carriage Assembly V0.1/mod/TAZ 5 X Carriage Assembly V0.1_minimal_flatCompatible.fcstd
100.0 x 12.0 x 128.6 mm

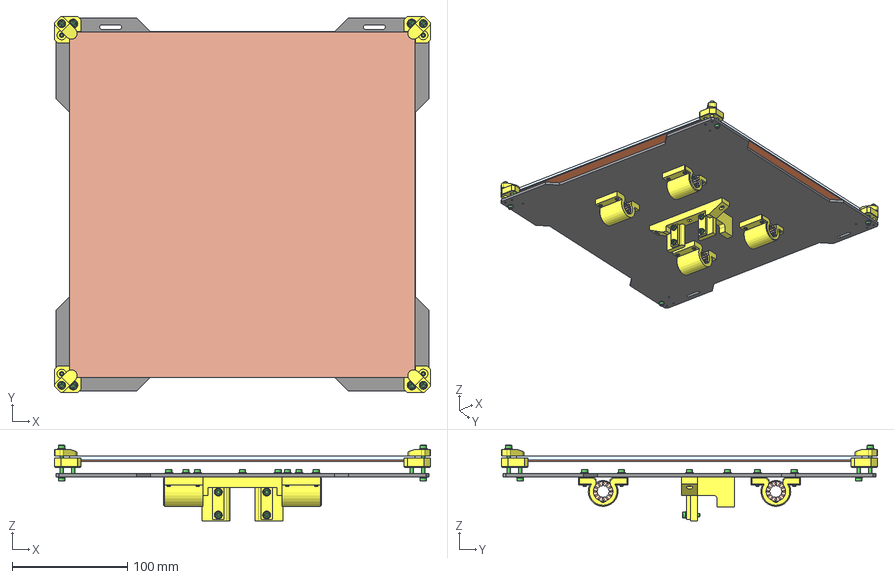
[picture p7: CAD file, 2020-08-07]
_experimental/0100-Bundle/0165-Slab-slabAlternative-binderClipShim/_ref/TAZ 5 Y Plate Assembly V0.21/orig/TAZ 5 Y Plate Assembly V0.21.fcstd
326.5 x 326.5 x 65.7 mm
bed_corner_2_5_01
bed_corner_2_5_02
bed_corner_2_5_03
bed_corner_2_5_04
Y_BeltMount_v2_3_01
bed_finger_2_1_01
bed_finger_2_1_02
bed_finger_2_1_03
bed_finger_2_1_04
Bearing_Holder_v1_1_b_01
Bearing_Holder_v1_1_b_02
Bearing_Holder_v1_1_b_03
Bearing_Holder_v1_1_b_04
BeltClamp_v2_02
BeltClamp_v2_01
_00mm_bed_mount_plate_revB_fc0_2_01
M3_washer_33
M3_washer_34
M3_washer_35
M3_washer_36
M3x12_SHCS_33
M3x12_SHCS_34
M3x12_SHCS_35
M3x12_SHCS_36
M3_washer_24
M3_washer_25
M3_washer_26
M3_washer_27
M3_washer_28
M3_washer_29
M3_washer_30
M3_washer_31
M3_washer_32
M3_washer_16
M3_washer_17
M3_washer_18
M3_washer_19
M3_washer_20
M3_washer_21
M3_washer_22
M3_washer_23
M3_washer_09
M3_washer_10
M3_washer_11
M3_washer_12
M3_washer_13
M3_washer_14
M3_washer_15
M3_washer_01
M3_washer_02
M3_washer_03
M3_washer_04
M3_washer_05
M3_washer_06
M3_washer_07
M3_washer_08
M3x12_SHCS_25
M3x12_SHCS_26
M3x12_SHCS_27
M3x12_SHCS_28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

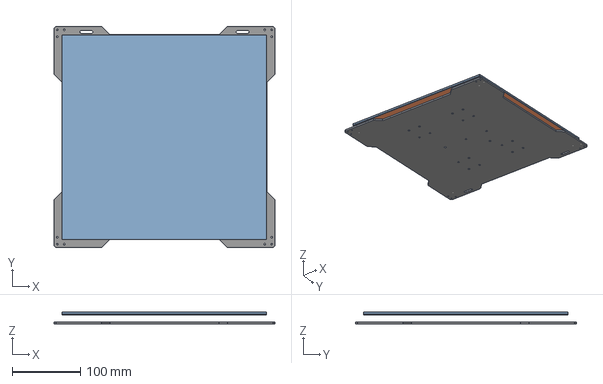
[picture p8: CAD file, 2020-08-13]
_experimental/0100-Bundle/0165-Slab-slabAlternative-binderClipShim/_ref/TAZ 5 Y Plate Assembly V0.21/mod/TAZ 5 Y Plate Assembly V0.21.step
324.0 x 324.0 x 18.1 mm

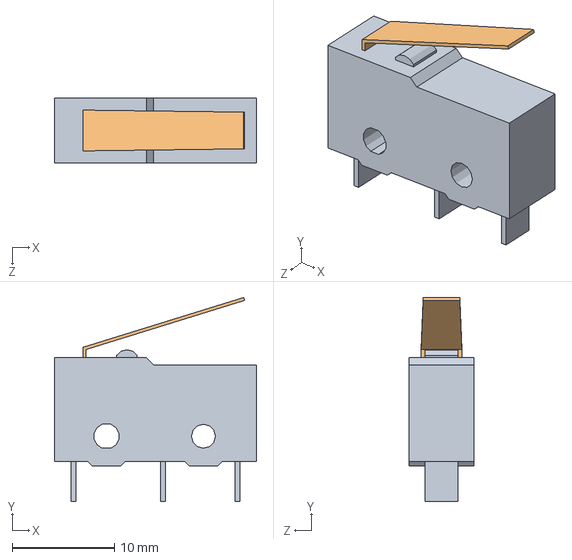
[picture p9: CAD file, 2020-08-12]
_experimental/_template/5000-Effectors/5058-LimitSwitch/_kit_Limit_Switch/_ref/LimitSwitch-xIsm9u/orig/OMRON_ss-5gl.SLDASM
19.8 x 20.0 x 6.40 mm
SS_01GL_E_BASE
SS_01GL_E_ACTUATOR

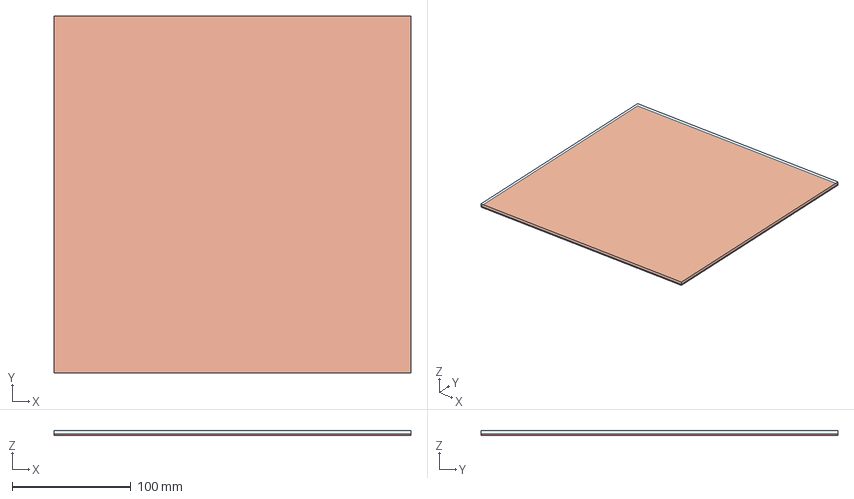
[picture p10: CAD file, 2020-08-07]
_experimental/0100-Bundle/0165-Slab-slabAlternative-binderClipShim/_ref/TAZ 5 Y Plate Assembly V0.21/mod/TAZ 5 Y Plate Assembly V0.21-slab_only.fcstd
300.0 x 300.0 x 4.50 mm
_00mm_heat_pad_01
_00mm_glass_01

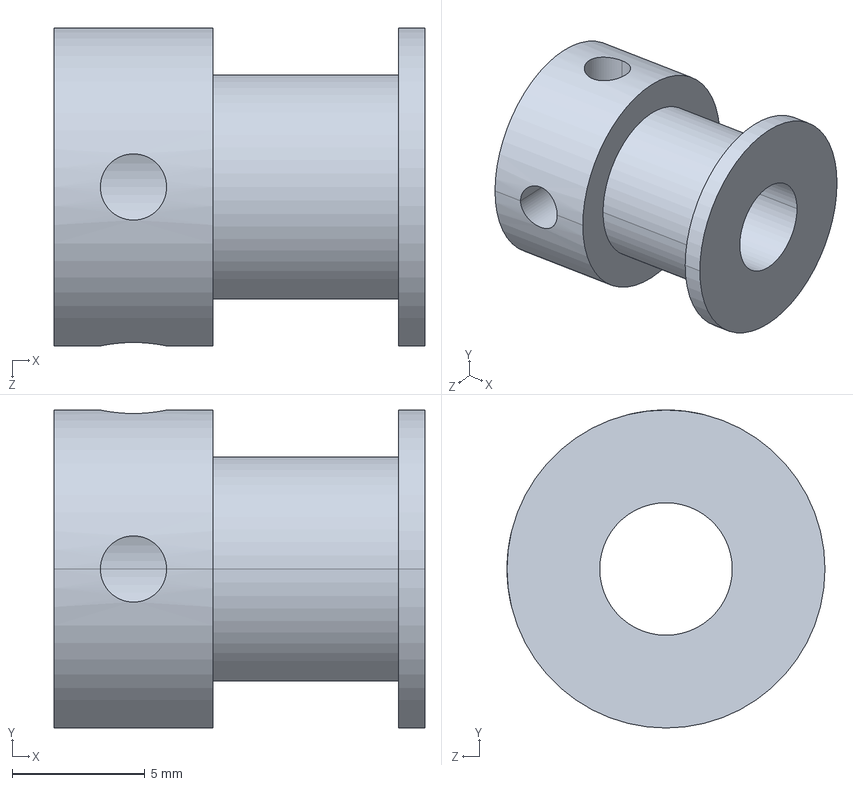
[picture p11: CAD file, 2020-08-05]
0100-Bundle/0110-Frames/AxisX/0100-Bundle/0150-Actuators/0100-Bundle/0151z-Thruster-Driver/_kit_Driver-Belt/5000-Effectors/5055-Pulleys/Pulleys-OpenBuilds_STEP/orig/GT2 Timing Pulley 14 Tooth.step
14.0 x 12.0 x 12.0 mm

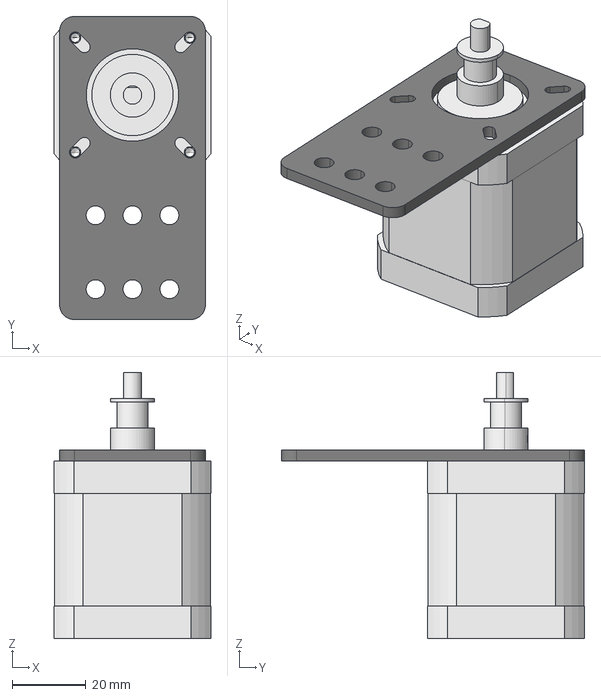
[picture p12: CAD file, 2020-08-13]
0100-Bundle/0110-Frames/AxisX/0100-Bundle/0150-Actuators/0100-Bundle/0151z-Thruster-Driver/_kit_Driver-Belt/Driver-Belt.step
42.4 x 82.0 x 72.0 mm

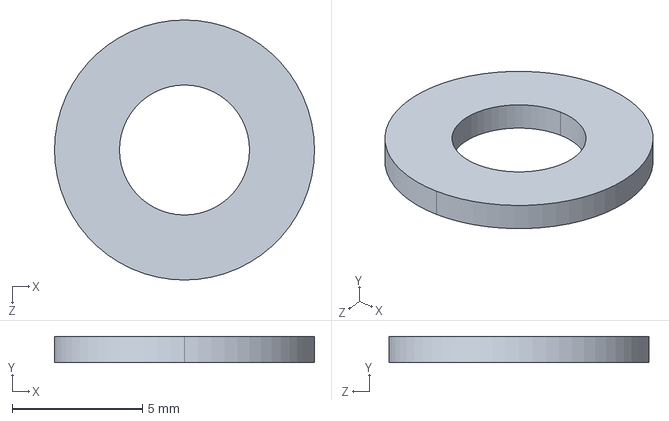
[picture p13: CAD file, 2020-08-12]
0100-Bundle/0110-Frames/AxisX/0100-Bundle/0150-Actuators/0100-Bundle/0151z-Thruster-Driver/_kit_Thruster-Belt/5000-Effectors/5051z-RotaryBearings-RotaryShims/RotaryBearings-RotaryShims-OpenBuilds_STE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
10.0 x 1.00 x 10.0 mm

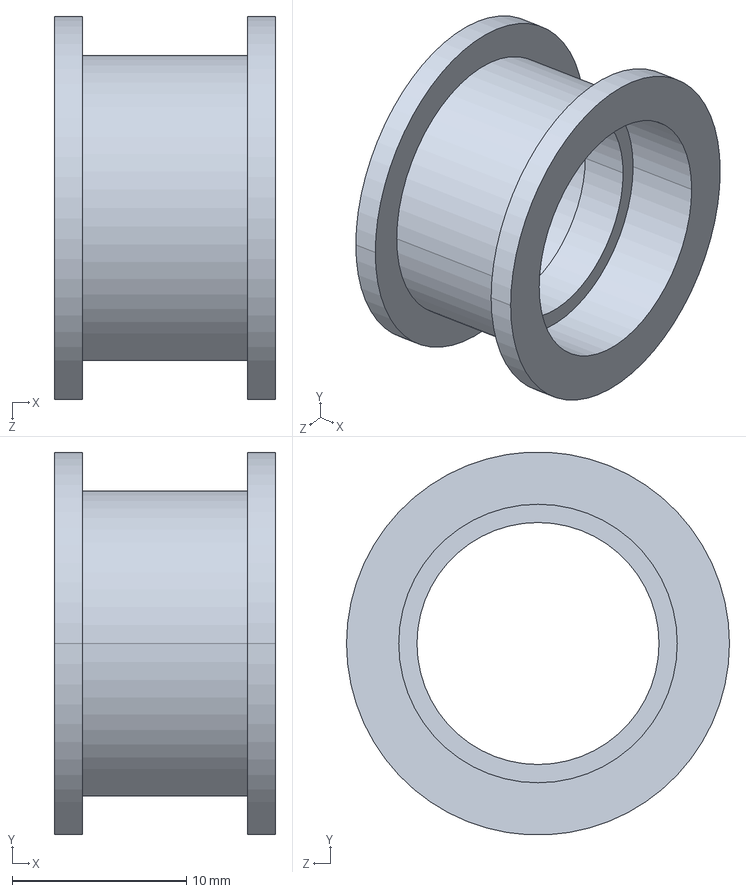
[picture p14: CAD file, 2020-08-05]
0100-Bundle/0110-Frames/AxisX/0100-Bundle/0150-Actuators/0100-Bundle/0151z-Thruster-Driver/_kit_Thruster-Belt/5000-Effectors/5055-Pulleys/Pulleys-OpenBuilds_STEP/orig/Smooth Idler Pulley Wheel.step
12.7 x 22.0 x 22.0 mm

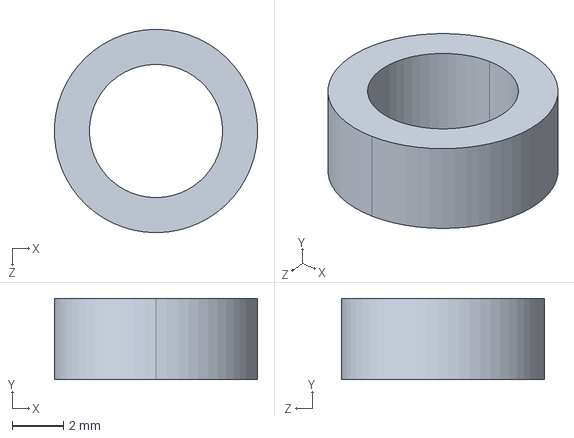
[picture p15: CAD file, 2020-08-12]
0100-Bundle/0110-Frames/AxisX/0100-Bundle/0150-Actuators/0100-Bundle/0151z-Thruster-Driver/_kit_Thruster-Belt/9000-Miscellaneous/9099-Misc/OpenBuilds_STEP/orig/Nylon Spacer 0.125in.step
7.93 x 3.17 x 7.94 mm

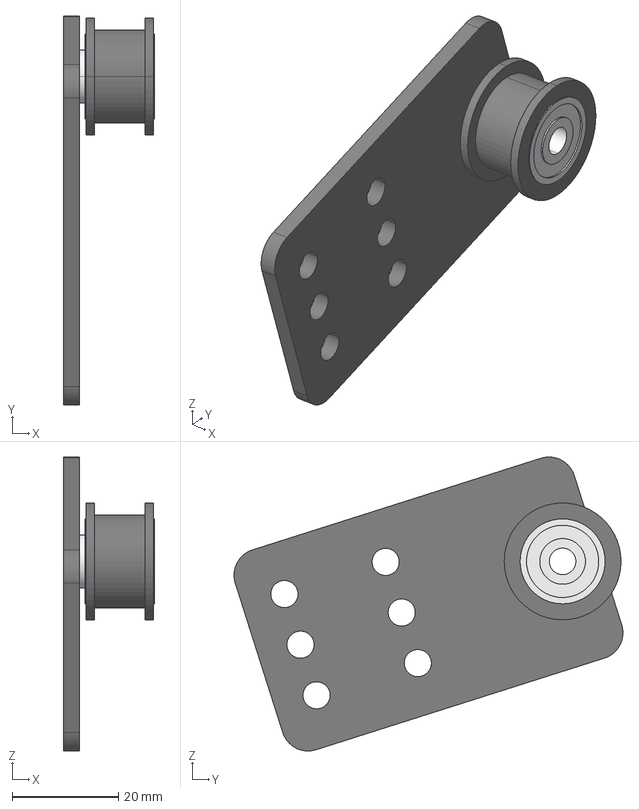
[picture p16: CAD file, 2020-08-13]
0100-Bundle/0110-Frames/AxisX/0100-Bundle/0150-Actuators/0100-Bundle/0151z-Thruster-Driver/_kit_Thruster-Belt/Thruster-Belt.step
17.1 x 73.2 x 55.4 mm

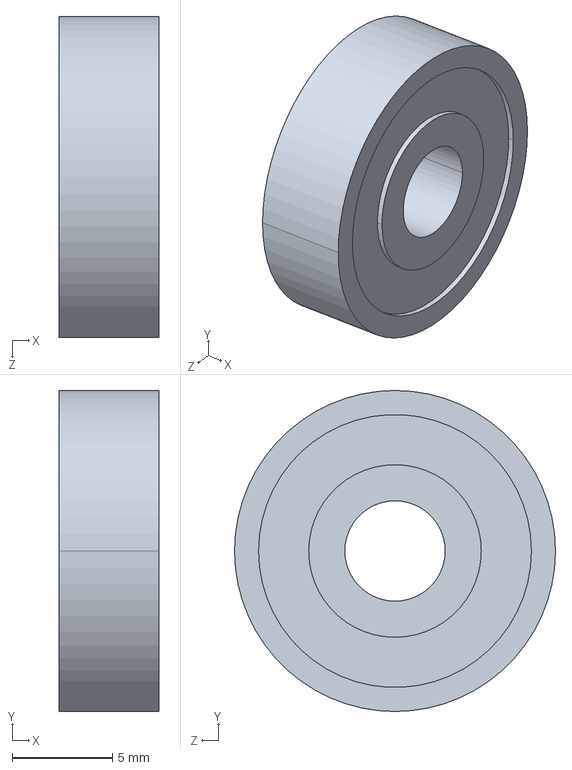
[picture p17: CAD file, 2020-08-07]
0100-Bundle/0110-Frames/AxisX/0100-Bundle/0150-Actuators/0151z-Thruster-Driver/_kit_Thruster-Belt/5000-Effectors/5051z-RotaryBearings-RotaryShims/Ball Bearing 5 x 16 x 5.step
5.00 x 16.0 x 16.0 mm

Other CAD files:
0100-Bundle/0110-Frames/AxisX/0100-Bundle/0150-Actuators/1100-Structural/1110z-Extrusions-Timbers/_resized/Extrusions-OpenBuilds_STEP/mod/V-Slot 20x60x760mm.step
0100-Bundle/0110-Frames/AxisX/0100-Bundle/0150-Actuators/_kit_Axis_X-Truck/9000-Miscellaneous/9095-frequent/Corner-OpenBuilds_STEP/orig/Black Angle Corner Connector.step
0100-Bundle/0110-Frames/AxisX/0100-Bundle/0150-Actuators/0100-Bundle/0151z-Thruster-Driver/_kit_Driver-Belt/Driver-Belt.fcstd
0100-Bundle/0110-Frames/AxisX/0100-Bundle/0150-Actuators/0100-Bundle/0151z-Thruster-Driver/_kit_Thruster-Belt/9000-Miscellaneous/9090z-Screws-Bolts/Screws-Bolts-OpenBuilds_STEP/orig/Nylon Insert Lock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
0100-Bundle/0110-Frames/AxisX/0100-Bundle/0150-Actuators/0100-Bundle/0151z-Thruster-Driver/_kit_Thruster-Belt/Thruster-Belt.fcstd
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

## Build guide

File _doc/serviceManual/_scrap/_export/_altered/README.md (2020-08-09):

# List

Idler Plate must be cut to smaller size - 'Threaded Rod Plate Nema 17-Idler' .

ACME threaded rods must be carefully sanded to exactly fit ball bearings. Ideally, this should be done in stages from rough to fine grit sand paper.

Excessive sanding will result in a loose fit between the bearing and threaded rod, leading to a variety of severe mechanical problems severely reducing print quality.

Cutting of threaded rods to length should be done after any diameter reduction by sanding, to allow for mistakes to be corrected.

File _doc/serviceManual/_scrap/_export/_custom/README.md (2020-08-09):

```
GantryPlate-Taz
XYplate
	* Ensures machine is assembled orthogonally - intended to provide flat surfaces and correct spacings.
	* Resists deformation more strongly than separate corner brackets - all three rotation axes constrained by large plates.
	* Flatness and hole spacing tight tolerance. Outline loose tolerance.

ShimFlexiblePreload-8mm
	* May reduce bearing failure rate - intended to spread load from possibly misaligned lock collar.
	* Omit if ambient temperature is to exceed 60C (ie. if within higher-temperature enclosure).
	* Loose tolerance. Surface defects tolerable. Less than solid infill preferred. High compressibility desired. Ideally 3D printed from transparent highly flexible material, possibly TPU or TPC.
	* May be substituted by neoprene foam.
```

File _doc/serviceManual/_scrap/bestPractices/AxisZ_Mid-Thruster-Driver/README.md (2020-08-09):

# Driver

## Preload

Lead screw (ACME Threaded Rod) *must* be pulled away from the motor by at least 2.5mm, under tension provided by flexible coupling, as the lock collar is tightened.

Preload is *required* to ensure accurate motion and prevent independent vibration.

If this step is necessary and omitted, theoretically, among other problems...
* Slab leveling may need to be performed frequently.
* Top surfaces of printed parts may appear to have incorrectly tall regions (warping without detaching from the slab).
* Visible surfaces on printed parts may appear rougher at long regions near the edges due to independent mechanical 'ringing'.

# Thruster

## Optional.

May be omitted entirely.

Intended to prevent the lead screw (ACME Threaded Rod) from moving freely along the X-axis, Y-axis, or downwards along the Z-axis.

May not be necessary. Wheels, being far more rigidly constrained than legacy bushings, should prevent lead screw from moving freely along the X-axis or Y-axis. Adequate driver preload should prevent lead screw from moving freely downwards along the Z-axis.

If this part is necessary and omitted, theoretically, among other problems...
* Misalignment of one printed layer from the next may occur. Such misalignment would manifest as a 'wavy' side-to-side appearance of a printed part from top to bottom.

## Optional.

May be omitted partially. Lock collar and all shims, including the metal and flexible shim, may be omitted.

Intended to prevent the lead screw (ACME Threaded Rod) from moving freely downwards along the Z-axis.

May not be necessary. Adequate driver preload should prevent lead screw from moving freely downwards along the Z-axis.

If this part is necessary and omitted, theoretically, among other problems...
* Slab leveling may need to be performed frequently.
* Visible surfaces on printed parts may appear unusually rough/ragged.

## Preload

Lock collar must be tightened at least 0.5mm further down the lead screw (ACME Threaded Rod) than required to meet the following metal shim. Otherwise, the lock washer and subsequent shims serve no purpose.

If this part is necessary and omitted, theoretically, among other problems...
* Slab leveling may need to be performed frequently.
* Visible surfaces on printed parts may appear unusually rough/ragged.

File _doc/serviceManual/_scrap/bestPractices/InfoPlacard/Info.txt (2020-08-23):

To be noted on a document attached to machine under waterproof enclosure.

MOTORS MUST HOLD WHILE CHANGING TOOL/FILAMENT OR Z-AXIS WILL BE BACKDRIVEN OUT OF ALIGNMENT!

Purple marked objects are intended for frequent user interaction, such as quickchange mount points.

Metalized tape shims are to be used to adjust Z-axis limit switch, and possibly also to adjust slab corner heights.

BAUDRATE		250000

microSteps/mm X/Y	114.29 or 114.79 (thermoplastic shrink compensation)
microsteps/mm Z		400

Motor current 1.7A or less if downgraded.
	Marlin/RAMBO firmware 255 'DIGIPOT_MOTOR_CURRENT' setting.

Marlin/RAMBO Known Stepper Driver Microstepping mode table...
#define MICROSTEP1 LOW,LOW
#define MICROSTEP2 HIGH,LOW
#define MICROSTEP4 LOW,HIGH
#define MICROSTEP8 HIGH,HIGH
#define MICROSTEP16 HIGH,HIGH

Marlin/RAMBO Known Endstop/Direction Configuration
#define INVERT_X_DIR false    // for LulzBot set to false
#define INVERT_Y_DIR true    // for LulzBot set to true
#define INVERT_Z_DIR false     // for LulzBot set to false
#define INVERT_E0_DIR true   // for standard LulzBot hotends set to true
#define INVERT_E1_DIR true    // for standard LulzBot hotends set to true
#define INVERT_E2_DIR true   // for standard LulzBot hotends set to true
#define X_HOME_DIR -1
#define Y_HOME_DIR 1
#define Z_HOME_DIR -1
const bool X_MIN_ENDSTOP_INVERTING = false; // set to true to invert the logic of the endstop.
const bool Y_MIN_ENDSTOP_INVERTING = false; // set to true to invert the logic of the endstop.
const bool Z_MIN_ENDSTOP_INVERTING = true; // set to true to invert the logic of the endstop.
const bool Z_PROBE_ENDSTOP_INVERTING = true; // set to true to invert the logic of the endstop.
const bool X_MAX_ENDSTOP_INVERTING = false; // set to true to invert the logic of the endstop.
const bool Y_MAX_ENDSTOP_INVERTING = false; // set to true to invert the logic of the endstop. USED FOR EMI ATTENUATION!
const bool Z_MAX_ENDSTOP_INVERTING = false; // set to true to invert the logic of the endstop.
#define X_MAX_POS 300
#define X_MIN_POS -20
#define Y_MAX_POS 303
#define Y_MIN_POS -20
#define Z_MAX_POS 270
#define Z_MIN_POS 0

Do not enable stepper release. Z-axis must hold while changing filament.
#define DEFAULT_STEPPER_DEACTIVE_TIME 60
#define SD_FINISHED_STEPPERRELEASE true

----- SAFETY NOTICES -----

DANGER! KEEP HANDS CLEAR
UNUSUAL HAZARDS - HIGH SPEED, HIGH RIGIDITY, HIGH HEAT!

ALWAYS INCLUDE SAFETY MARGINS WITH ENDSTOP AND PROBE!
RIGIDITY AND FORCE SUFFICIENT TO CAUSE PERMANENT DAMAGE!
BEWARE BROKEN GLASS!

AVOID CONTACT WITH HIGH-VOLTAGE OR WET CONTACT WITH LOW-VOLTAGE!

INDUSTRIAL OEM EQUIPMENT!
Distributed WITHOUT ANY WARRANTY, without even the implied warranty of MERCHANTABILITY or FITNESS FOR A PARTICULAR PURPOSE .

----- Copyright Notices -----
Several authors may have GPL copyright claims, consequently, incorporated source material must be include in any distribution - mirage335, AlephObjects, MarlinFirmware .
"This design incorporates OpenBuilds, LLC design work(s) shared Open Source under the CC BY-SA 4.0 License."
Other third party material may be incorporated as well.
Please see a copy of the relevant source repositories, which should have been included entirely due to the large set of GPL licensed source incorporated.

----- Remove this line and below if not experimental. -----
Experimental. Items may be swapped. Especially, motors and chasis cooling.

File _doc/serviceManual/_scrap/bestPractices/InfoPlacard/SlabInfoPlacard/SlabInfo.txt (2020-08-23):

To be noted on a document attached to slab under waterproof enclosure.

Purple marked objects are intended for frequent user interaction, such as quickchange mount points.

Marlin/RAMBO Known Heater Settings
// 7 is 100k Honeywell thermistor 135-104LAG-J01 (4.7k pullup)
#define TEMP_SENSOR_BED 7
#define BED_MAXTEMP 150
#define MAX_BED_POWER 206 (or less if necessary to protect PSU)
#define DEFAULT_bedKp 162
#define DEFAULT_bedKi 17
#define DEFAULT_bedKd 378

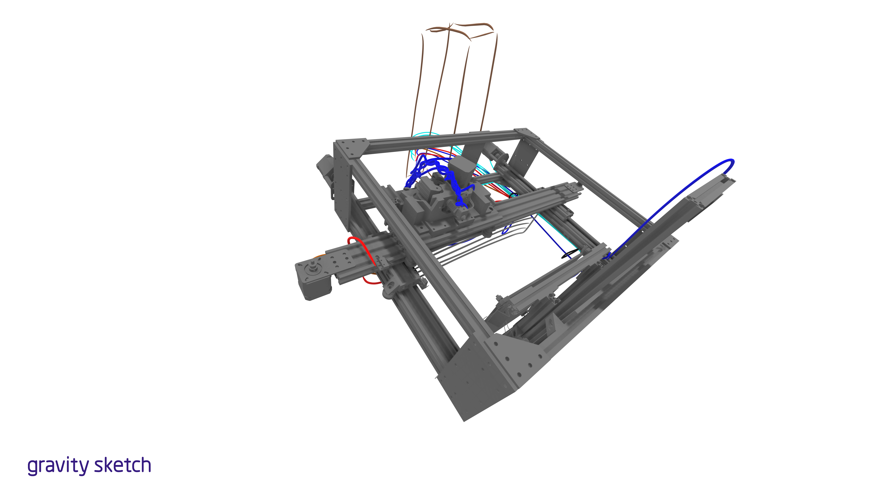
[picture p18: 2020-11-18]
_doc/VR/TazIntermediate-Cabling-GravitySketch/_iterations/1/png/wiring_2020-11-18-01-18-502.png

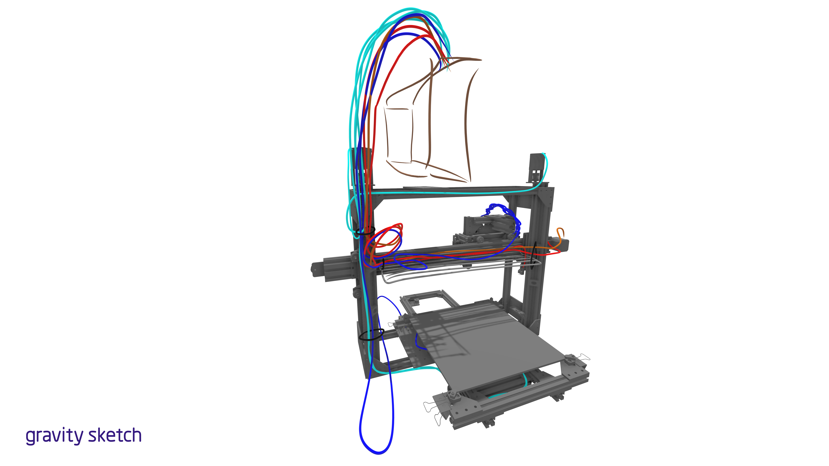
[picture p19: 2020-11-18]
_doc/VR/TazIntermediate-Cabling-GravitySketch/_iterations/1/png/wiring_2020-11-18-01-18-493.png

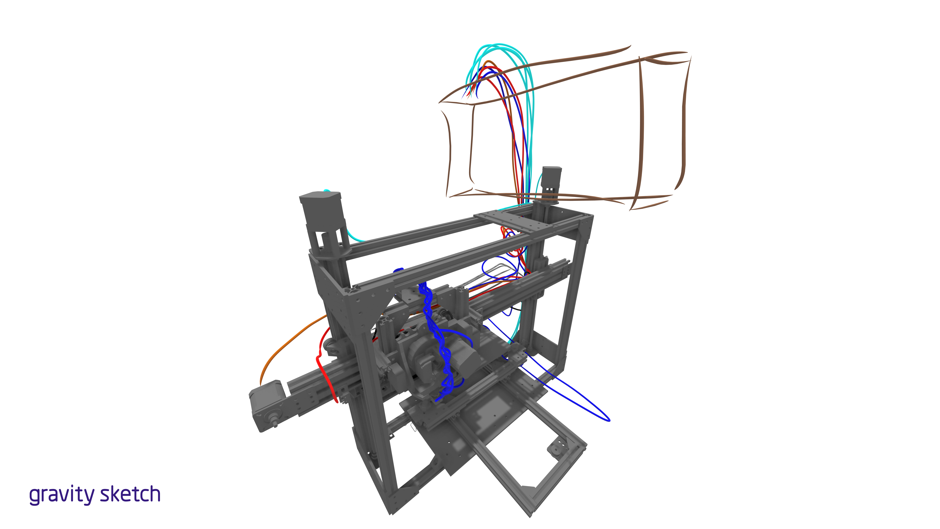
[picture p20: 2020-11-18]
_doc/VR/TazIntermediate-Cabling-GravitySketch/_iterations/1/png/wiring_2020-11-18-01-18-501.png

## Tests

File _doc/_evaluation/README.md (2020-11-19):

WARNING: Evaluation files have been created/distributed solely to identify and document defects . Do not rely on these files for any production use.

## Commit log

2020-08-07 Basic experimental slab assembly.
    [20series-1x1-60mm.fcstd, 20series-1x1-crossbar.fcstd, 20series-1x1-postX.fcstd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]
2020-08-07 Draft slab.
    [20series-1x1-60mm.fcstd, 20series-1x1-crossbar.fcstd, 20series-1x1-postX.fcstd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]
2020-08-07 Frame brackets and AxisZ linear rail position.
    [AxisZ_Mid.fcstd, BeltAnchor-SledY.fcstd, Slab.fcstd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]
2020-08-09 Additional axes, tool quickchange, documentation.
    [8mm Acme Nut Plate.step, Aluminum Spacer 1.5in.step, Aluminum Spacer 6mm.step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]
2020-08-09 Draft CAD model. LulzBot_Extruder tool integrated for reference.
    [Hexagon Hotend_1.75mm v3.iges, Hexagon Hotend_1.75mm v3.step, Hexagon Hotend_1.f3d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]
2020-08-09 Include LulzBot extruder carriage for reference.
    [LulzBot_Extruder-LulzBot_Mount-Carriage.fcstd, TAZ 5 X Carriage Assembly V0.1.fcstd, TAZ 5 X Carriage Assembly V0.1_minimal.fcstd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]
2020-08-10 Draft. Correct tool quick change bracket.
    [AxisZ_Mid.fcstd, Axis_X-Actuator.fcstd, Axis_X-Truck.fcstd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]
2020-08-11 Kit - Vwheel-Corner .
    [20series-1x1-60mm.fcstd, 20series-1x1-crossbar.fcstd, 20series-1x1-postX.fcstd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]
2020-08-11 Allow axis motion - top model constraints.
    [AxisZ_Mid-Stationary.fcstd, AxisZ_Mid.fcstd, AxisZ_Truck-Double.fcstd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]
2020-08-11 Correct Vwheel-Corner-EccentricThinHex assemblies.
    [Aluminum Spacer 6mm.step, AxisZ_Truck-Double.fcstd, Axis_X-Truck.fcstd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]
2020-08-11 Moved Vwheel related files.
    [Ball Bearing 5 x 16 x 5.step, Eccentric Spacer 6mm.step, Nylon Insert Lock Nut M5.step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]
2020-08-12 Belt thruster-driver kits.
    [AxisY.fcstd, Axis_X-Actuator.fcstd, Ball Bearing 5 x 16 x 5.step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]
2020-08-12 Limit switches. Complete OpenBuilds Step Library.
    [120 Angle Tee Nut.STEP, 135 Angle Tee Nut.STEP, 2 Way Tee Nut.STEP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]
2020-08-13 LulzBotExtruder_Adapted .
    [Aluminum Spacer 6mm.step, Axis_X-Truck.fcstd, Axis_X-Truck.step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]
2020-08-13 Optional legacy slab corner mounts.
    [20series-1x1-60mm.fcstd, 20series-1x1-60mm.step, 20series-1x1-crossbar.fcstd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]
2020-08-20 BOM - WIP.
    [LimitSwitch.fcstd, TazIntermediate.fcstd, _bom.csv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]
2020-08-23 Draft BOM.
    [_bom.csv, _consolidated_bom.csv, bins.ods]
2020-08-23 Stock machine salvage estimates.
    [bins.ods]
2020-08-23 Draft legible BOM.
    [_bom.csv, _consolidated_bom.csv, bins.ods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]
2020-08-23 Draft materials list - BOM, etc.
    [LulzBotExtruder_Carriage_Block.stl, LulzBotExtruder_Plate.dxf, ShimFlexiblePreload-8mm.stl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]
